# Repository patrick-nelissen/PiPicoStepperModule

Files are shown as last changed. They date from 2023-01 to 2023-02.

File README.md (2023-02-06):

# Pi Pico Stepper Module
Stepper Motor motion controller with trapezoidal motion profile and RS485 interface.

## ABOUT

This microPython application runs on a Raspberry Pi Pico (RP2040) and is controlling a Stepper Motor Driver Module. The hardware is a TB6600 derivative from Toshiba, specifically the TB67S109AFTG.

The Module's enclosure is re-engineered and modified to make room for:
1. The Pi Pico board with USB access
2. DC/DC Converter to power the Pi Pico
3. A serial RS-485 half-duplex converter and connectivity
4. Opto Coupler connectivity to home the controlled axis
5. PCB Screw Terminal Block receiver for external connectivity of item 3. and 4.

## SOFTWARE

### MotionControl.py
This module is the top-level module that communicates with the master on the RS485 serial interface. It monitors the RS485 bus for commands and queries and acts on those that are intended for its hardware module.

### lib/CommandQueue.py
This module manages the mimicking of the AllMotion protocol as specified in Command_Set.pdf in the \Hardware\Datasheets folder.

### lib/StepConfiguration/py
This module manages configuration parameters specific to this hardware.
These include, but are not limited to module number (RS485 is a multi-drop communication bus), but also defaults used by StepControl.py
 
### lib/StepControl.py
This module manages the control of the low-level stepper hardware's ENABLE, DIRECTION, and STEP signals.
It takes speed, acceleration, move distance, step size etc as input, and then calculates a pulse delay table to create and execute a trapezoidal motion profile.

### Utilities

#### Utilities/SendRs485Command.py
Run RS485 interface on Host.

#### Utilities/UsbCommand.py
Use the REPL Host interface available on the USB of Pi Pico

## HARDWARE

The hardware files consist of:
1. Build Instructions
2. Wiring instruction for wiring the Pi Pico to:
	- TB6600, 4A Stepper Motor Driver 4A for Nema 17 23 and 34 Stepper Motor
      https://www.amazon.com/dp/B08PKJG2ND
	- SparkFun Transceiver Breakout - RS-485
      https://www.sparkfun.com/products/10124
	- 6-Pin 5.08mm Pitch Male Female PCB Screw Terminal Block
      https://www.amazon.com/dp/B093DMG1QZ
	- IR Slotted Optical Optocoupler, 3.3V to 5V
      https://www.amazon.com/dp/B09W5KWFV6
    - MP1584EN DC-DC, 3A Converter, 24V to 12V - 3V
      https://www.amazon.com/dp/B08247LRYS
3. Datasheets for:
	- TB67S109AFTG stepper controller
	- AllMotion Command Interface
4. CAD design files for the re-engineered enclosure in format:
	- SolidWorks .sldpt
	- .step files
	- .png file depicting the design
5. 3D print files in:
	- .3mf format (PrusaSlicer 2.5 export)
	- .stl file
	- .step file (see CAD)
	- .png depicting the "Paint On Supports" that are recommended

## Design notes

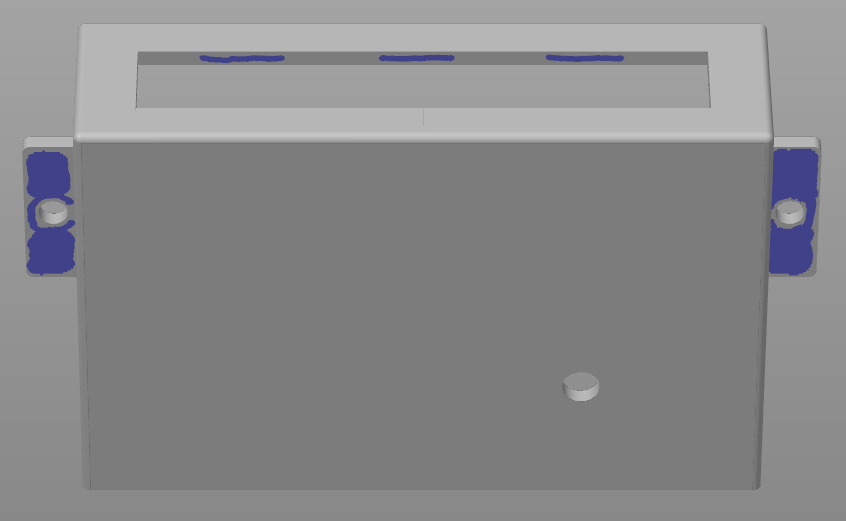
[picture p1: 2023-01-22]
Hardware/3DPrint/PaintOnSupports.png

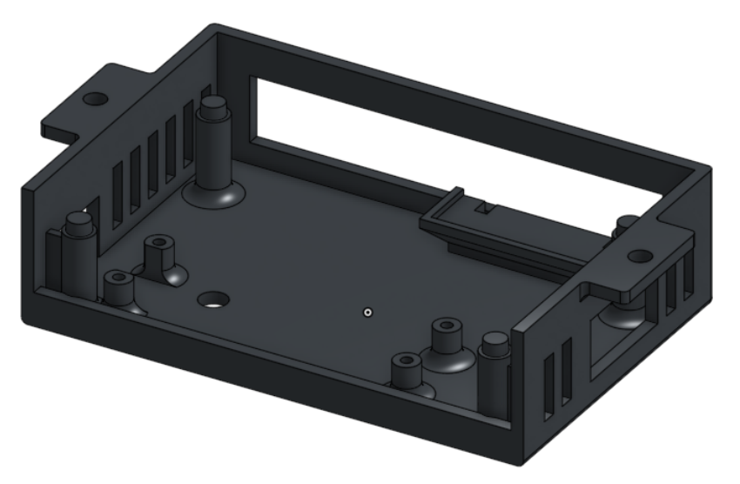
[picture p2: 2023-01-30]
Hardware/CAD/Overview.png

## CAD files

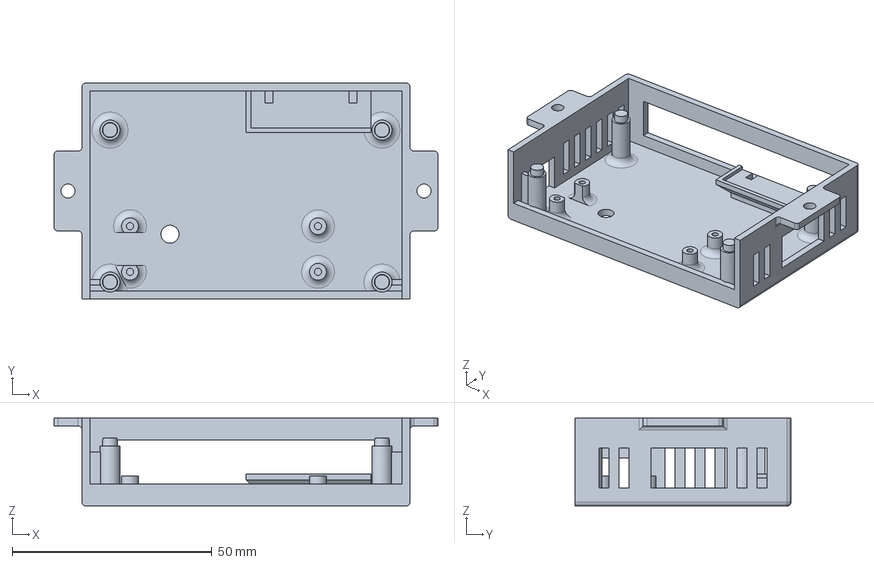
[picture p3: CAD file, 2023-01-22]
Hardware/CAD/MicroStepperEnclosure V7.2.step
96.0 x 54.0 x 22.0 mm

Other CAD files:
Hardware/3DPrint/MicroStepperEnclosure V7.2.3mf
Hardware/CAD/MicroStepperEnclosure V7.2.sldprt

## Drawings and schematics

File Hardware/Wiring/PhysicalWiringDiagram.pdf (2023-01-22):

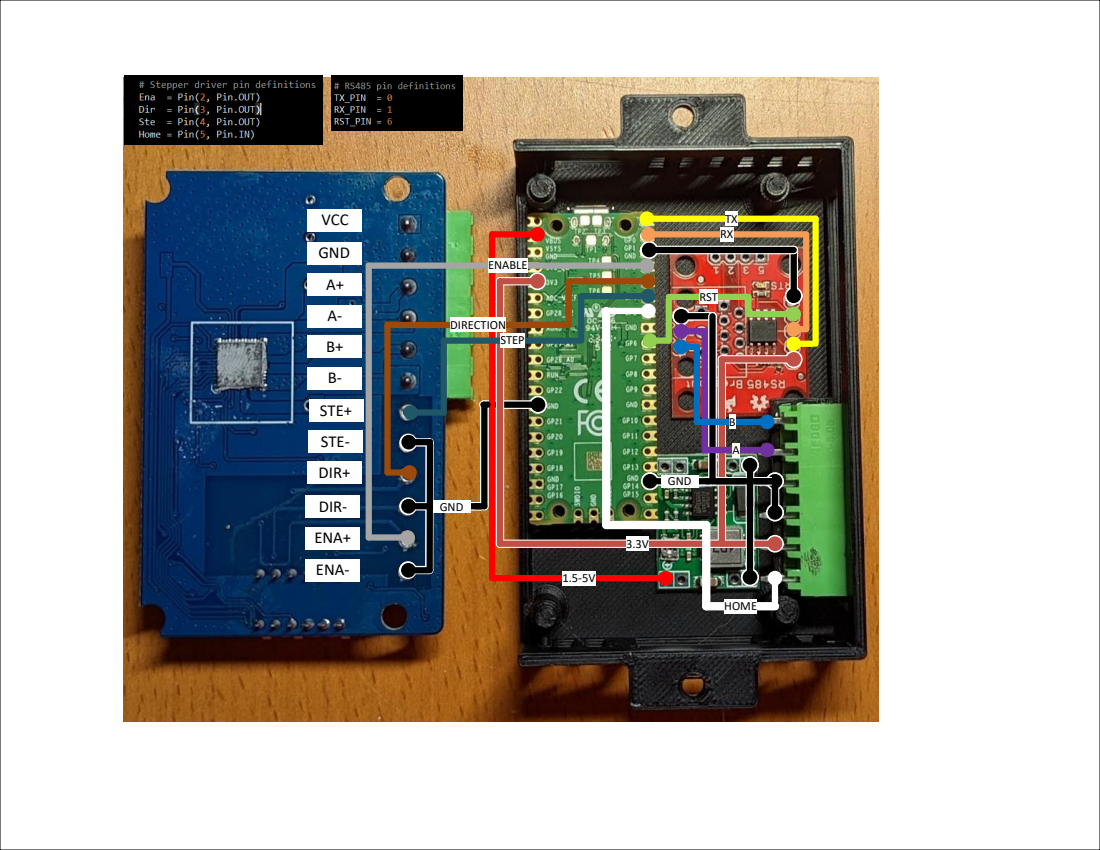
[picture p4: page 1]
VCC; GND; STE+; STE-; DIR+; DIR-; ENA+; ENA-; RST; ENABLE; DIRECTION STEP; HOME

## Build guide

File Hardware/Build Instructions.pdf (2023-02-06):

BUILD INSTRUCTIONS

The document documents steps to turn the standard stepper hardware, as bought on Amazon, into a Pi Pico controlled/enclosed stepper motion controller with RS485 interface.

1. Open the standard stepper controller. Expect an aluminum spacer to bridge the gap between the TB67S109AFTG IC and the aluminum heatsink. If you are lucky some thermal compound and/or blob of silicon will keep this spacer in place. For sure you will need to apply thermal compound between this spacer and the heatsink. Non was present on mine.

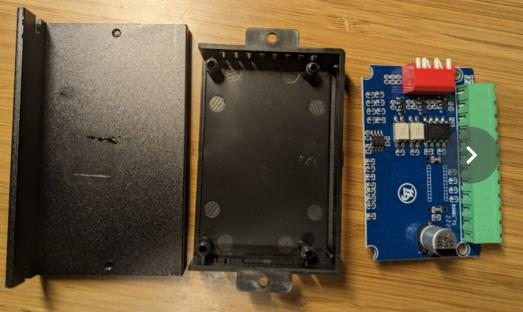
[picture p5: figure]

2. Remove one half of the terminal block as depicted below. I used a Dremel to separate the main connector body. Then cutters to free up the individual connectors. This makes it easy to push/remove them when heating up with a soldering iron. Clean the pads.

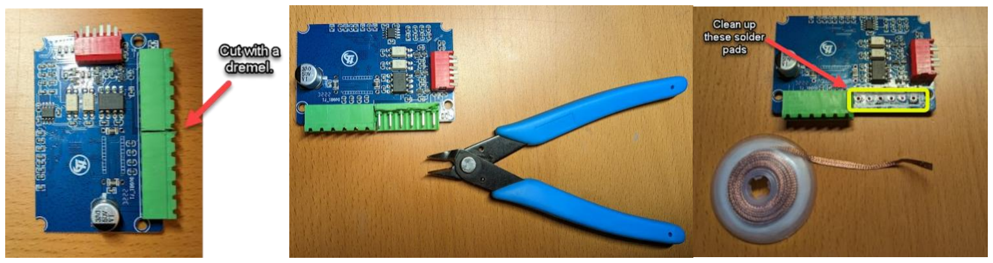
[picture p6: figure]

3. Print the new enclosure. CAD files and print files are provided. I used PLA. The new enclosure is a little taller to make room for the Pi Pico. It has PCB stand-off for the PiPico, a hole on the side to allow Pi Pico USB access, and a pedistole for the terminal block for external RS485 and optocoupler connectivity .

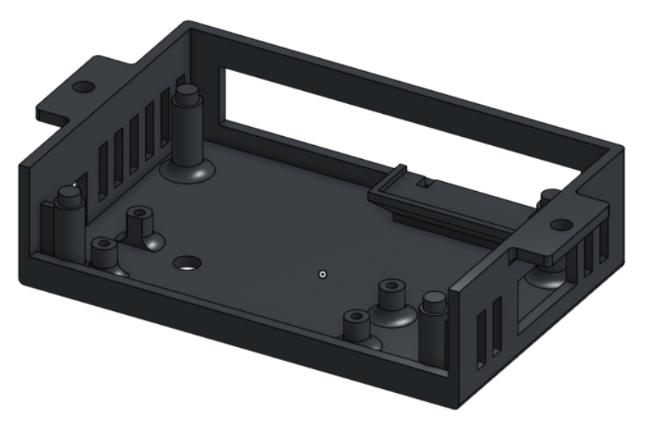
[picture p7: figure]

4. Glue the terminal block on top of the pedestal with some epoxy.
5. Mount the Pi Pico with M2 screws to the dedicated stand-offs.
6. Perform all the wiring per wiring diagram. I used 30AWG enameled copper wire. You can use tiny colored glass seed beads for color coding ;o).

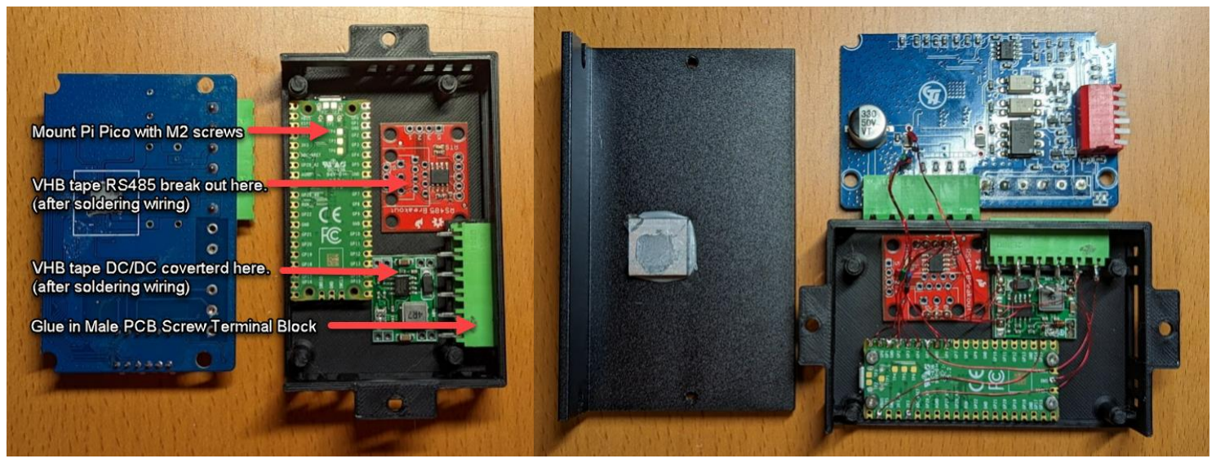
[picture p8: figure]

7. After wiring is completed, attached the DC/DC and RS485 converter PCB to the ceiling of the enclosure with double sided VHB tape.

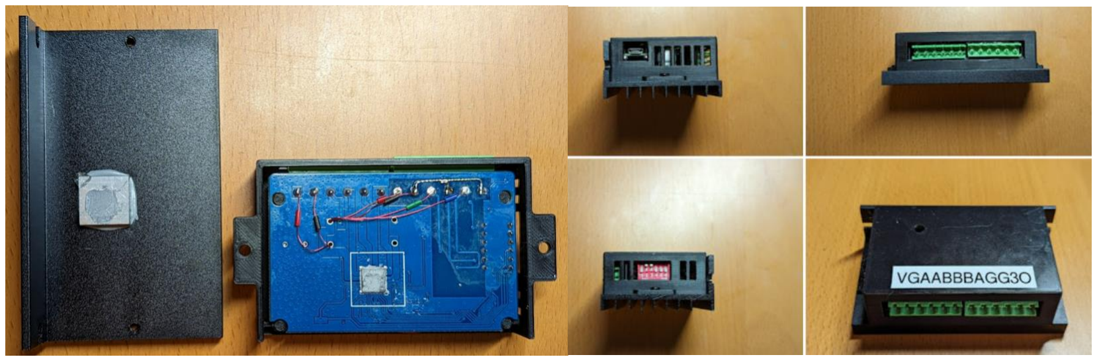
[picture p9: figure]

8. Don’t forget to add additional thermal compound when needed.

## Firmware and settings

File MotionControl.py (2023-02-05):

#  __  __       _   _              _____            _             _               
# |  \/  |     | | (_)            / ____|          | |           | |              
# | \  / | ___ | |_ _  ___  _ __ | |     ___  _ __ | |_ _ __ ___ | |  _ __  _   _ 
# | |\/| |/ _ \| __| |/ _ \| '_ \| |    / _ \| '_ \| __| '__/ _ \| | | '_ \| | | |
# | |  | | (_) | |_| | (_) | | | | |___| (_) | | | | |_| | | (_) | |_| |_) | |_| |
# |_|  |_|\___/ \__|_|\___/|_| |_|\_____\___/|_| |_|\__|_|  \___/|_(_) .__/ \__, |
#                                                                    | |     __/ |
#                                                                    |_|    |___/ 

import machine
from machine import Pin, UART
from time import sleep_ms
from CommandQueue import CommandSequence


# RS485 pin definitions
TX_PIN  = 0
RX_PIN  = 1
RST_PIN = 6  

# Define UART
uart0 =UART(0, baudrate=57600, bits=8, parity=None, stop=1, tx=Pin(TX_PIN), rx=Pin(RX_PIN))

# Define RST (Request To Transmitt)
RST  = Pin(RST_PIN, Pin.OUT)

# Flush serial buffer
def flushSerial(uart):
    while uart.any():
        uart.read(1)

# Set RST HIGH to transmit data
def  transmitData():
    RST.value(1)

# Set RST LOW to receive data
def receiveData():
    RST.value(0)      

# Command reply status
UNKNOWN     = -1 # Unknown status
NO_ERROR    =  0 # No error
INIT_ERROR  =  1 # Initialization error
BAD_COMMAND =  2 # Bad Command
OP_OO_RANGE =  3 # Operand out of range


# Start with listening
receiveData()

# Flush startup garbage from serial buffer
flushSerial(uart0)

myQueue = CommandSequence()

while True:
    
    commandReceived = False
    RxStatus = UNKNOWN 

    RxStr = uart0.read()
    if RxStr != None:
        # Decode byte string to character string
        RxStr=RxStr.decode('utf-8', 'replace')
        commandReceived = True
        
        # Command or query for me?
        if myQueue.CommandOrQueryForMe(RxStr) :
            
            # Valid Command?
            if myQueue.ValidCommand(RxStr):
                # Add to command queue
                myQueue.AddToQueue(RxStr)
                RxStatus = NO_ERROR
                
            # Valid Query?    
            elif myQueue.ValidQuery(RxStr):
                # Get the reply value
                RxStatus = myQueue.GetQueueReply(RxStr)
                
            else:
                RxStatus = BAD_COMMAND
                
            # Print the queue
            myQueue.Print()
           
    
    # Acknowledge Command received
    if commandReceived :
                
        # Switch RS485 levelshifter to transmit mode
        transmitData()
        
        # Write the RxStatus
        uart0.write(str(RxStatus))

        # Give the hardware some time to kick out this data
        sleep_ms(1)
        
        # Switch RS485 levelshifter back to receive mode
        receiveData()
        
        # Flush the uart in case the TX->RX caused some noise
        flushSerial(uart0)

        # Did we get a (R)un command?
        if myQueue.RunCommand(RxStr):
            # Execute the queue of commands
            myQueue.ExecCommandQueue()

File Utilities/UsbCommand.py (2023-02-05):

#  _    _     _      _____                                          _               
# | |  | |   | |    / ____|                                        | |              
# | |  | |___| |__ | |     ___  _ __ ___  _ __ ___   __ _ _ __   __| |  _ __  _   _ 
# | |  | / __| '_ \| |    / _ \| '_ ` _ \| '_ ` _ \ / _` | '_ \ / _` | | '_ \| | | |
# | |__| \__ \ |_) | |___| (_) | | | | | | | | | | | (_| | | | | (_| |_| |_) | |_| |
#  \____/|___/_.__/ \_____\___/|_| |_| |_|_| |_| |_|\__,_|_| |_|\__,_(_) .__/ \__, |
#                                                                     | |     __/ |
#                                                                     |_|    |___/ 
# Use the REPL interface instead of thr RS485 to send Allmotion Style commands
#
import machine
from machine import Pin, UART
from time import sleep_ms
from CommandQueue import CommandSequence

# Command reply status
UNKNOWN     = -1 # Unknown status
NO_ERROR    =  0 # No error
INIT_ERROR  =  1 # Initialization error
BAD_COMMAND =  2 # Bad Command
OP_OO_RANGE =  3 # Operand out of range

# Get a Command Sequence object
myQueue = CommandSequence()

while True:
    
    CmdStatus = UNKNOWN 

    # get keyboard input
    keyboardInput = input("Enter Command: ")
    if keyboardInput == "exit":
        exit()
    else:
        CmdStr = bytes(keyboardInput, "utf-8")
        
    if CmdStr != None:
        # Decode byte string to character string
        CmdStr=CmdStr.decode('utf-8', 'replace')
        
        # Command or query for me?
        if myQueue.CommandOrQueryForMe(CmdStr) :
            
            # Valid Command?
            if myQueue.ValidCommand(CmdStr):
                # Add to command queue
                myQueue.AddToQueue(CmdStr)
                CmdStatus = NO_ERROR
                
            # Valid Query?    
            elif myQueue.ValidQuery(CmdStr):
                # Get the reply value
                CmdStatus = myQueue.GetQueueReply(CmdStr)
                
            else:
                CmdStatus = BAD_COMMAND
                
            # Print the queue
            myQueue.Print()
           
        # Did we get a (R)un command?
        if myQueue.RunCommand(CmdStr):
            # Execute the queue of commands
            myQueue.ExecCommandQueue()
            
        print("Status: ", CmdStatus)

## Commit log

2023-01-21 Fix byte string conversion and lower default vmax
    [MotionControl.py]
2023-01-22 Increase default velocity
2023-01-22 Upload 3D Print files
    -.3MF Prusa Project File
    -.STL File
    -Depicted Support Locations
2023-01-22 Upload overview of wiring and components placement within printed enclosure
    -Visio File
    -.pdf export
2023-01-22 Opload .3mf file
    [MicroStepperEnclosure V7.2.3mf]
2023-01-22 Upload CAD files
    - .step format
    - SolidWorks format
    - Overview .png format
    [MicroStepperEnclosure V7.2.sldprt, MicroStepperEnclosure V7.2.step]
2023-01-23 Upload Driver Hardware specification
2023-02-05 Upload REPL command interface
    - Use the REPL command interface to issue Allmotion style commands instead of RS485
    [UsbCommand.py]
